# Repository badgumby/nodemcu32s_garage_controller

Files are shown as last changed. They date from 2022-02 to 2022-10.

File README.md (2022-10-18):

# NodeMCU-32s Garage Controller

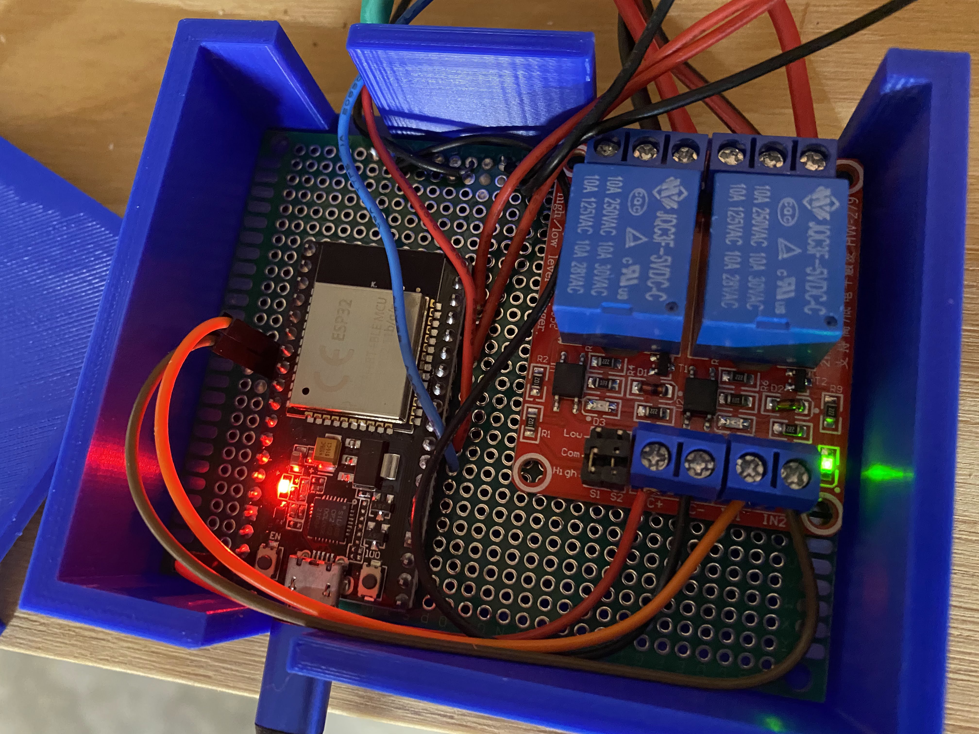
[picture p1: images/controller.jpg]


This project is still a WIP, so the code is yet to be optimized. The goal is to turn my two regular garage doors into "smart" garage doors. This controller will be the base platform using a NodeMCU-32s (or similarly cloned SoC).

## Materials

These are the items you may need to purchase to build this project.

### Devices/Sensors

- ESP32 Development Board
  - I used this one [KeeYees Development Board - ESP-WROOM-32 Chip](https://www.amazon.com/dp/B07QCP2451?psc=1&ref=ppx_yo2_dt_b_product_details)
  - But I also have this one, and it is better [DOIT DEVIT V1 ESP32-WROOM-32 Development Board](https://www.amazon.com/dp/B084KWNMM4?psc=1&ref=ppx_yo2_dt_b_product_details)

- Two magnetic reed switches
  - Similar item on Amazon: [Gikfun MC-38 Wired Door Sensor Magnetic Switch](https://www.amazon.com/dp/B0154PTDFI?psc=1&ref=ppx_yo2_dt_b_product_details)

- Two 5mm green LEDs (you can use pre-soldered LEDs with resistors, I believe mine were 460 ohm.)
  - Similar item on Amazon: [EDGELEC 56pcs (7 Colors x 8pcs)](https://www.amazon.com/EDGELEC-LED-Emitting-Assorted-Warm-White/dp/B07W4H66LR/)

- One 2-channel 5VDC relay module (high trigger)
  - Similar item on Amazon: [2 pcs 5V 2 Channel DC 5V Relay Module with Optocoupler High/Low Level Trigger](https://www.amazon.com/dp/B079FGPC9Y?psc=1&ref=ppx_yo2_dt_b_product_details)

### Misc Materials

- Speaker wire
  - Run from the relay to the garage door button sockets.
  - Similar item on Amazon: [TYUMEN 100FT 16 Gauge 2pin 2 Color Red Black Cable](https://www.amazon.com/dp/B07SG23DT1?psc=1&ref=ppx_yo2_dt_b_product_details)

- Printed circuit board
  - Just a generic PCB large enough to accommodate solder points for LEDs, relay leads, etc.
  - Similar item set on Amazon: [ELEGOO 32 Pcs Double Sided PCB Board Prototype Kit](https://www.amazon.com/dp/B072Z7Y19F?psc=1&ref=ppx_yo2_dt_b_product_details)

- 3D printer filament
  - The case for this project has been 3D printed, and I have provided the models along with the codebase. Please see the [Enclosure](#enclosure) section below.

## Schematic

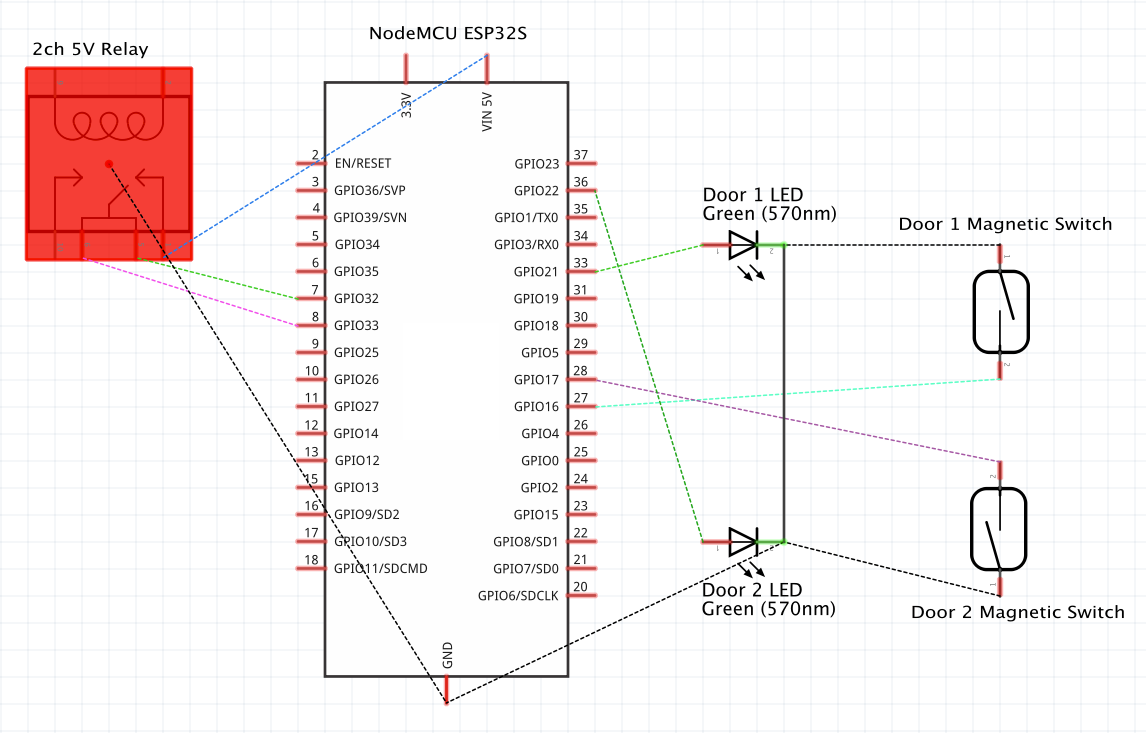
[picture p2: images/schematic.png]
Basic Schematic


Here is the schematic (created using Fritzing). Please note, the schematic does not have any resistors for the LEDs. This is because the LEDs I am using are pre-wired, and already have the correct resistors added for this voltage/amperage. Just don't forget to add some to your LEDs if you are not using pre-wired LEDs.

## Enclosure

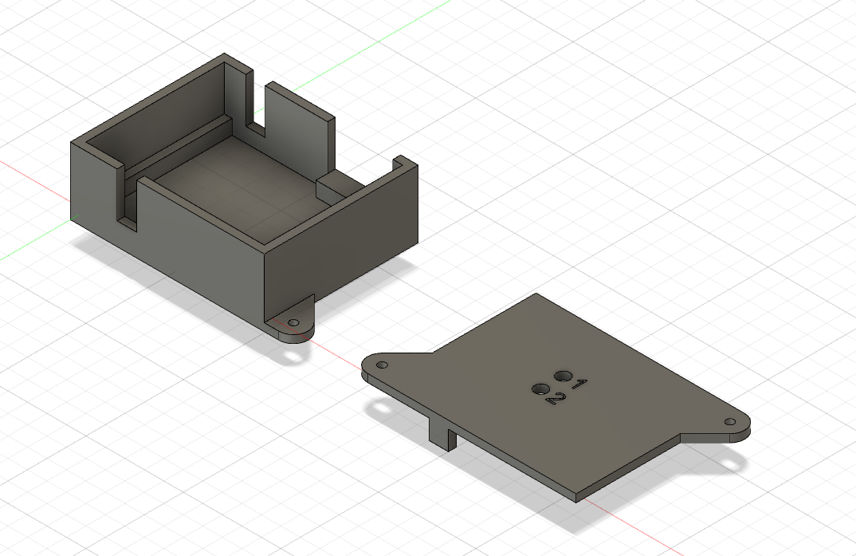
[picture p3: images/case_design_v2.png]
Fusion 360 model - v2


In this project, you will find the [STL files](/enclosure/STL/) for the top and bottom of the case, as well as, the [Fusion 360 model](/enclosure/Fusion%20360/) file. These can be used to 3D print the enclosure, or can be modified to fit your own project. It was designed around the 7cm x 9cm PCB linked in the [Misc Materials](#misc-materials) section above.

### 3D Print Settings

---

I have a Creality Ender 3 v2 with an upgraded Micro Swiss all-metal hotend, and these are the settings I used to print the enclosure (and most other things) in the [Cura slicing software](https://ultimaker.com/software/ultimaker-cura).

- Quality
  - Layer Height: 0.16 mm
  - Initial Layer Height: 0.2 mm
  - Line Width: 0.4 mm
  - Initial Layer Line Width: 100%
- Walls
  - Wall Thickness: 1.2 mm
    - Wall Line Count 3
  - Optimize Wall Printing Order: YES
  - Fill Gaps Between Walls: Everywhere
  - Horizontal Expansion: 0 mm
- Top/Bottom
  - Top/Bottom Thickness: 0.84 mm
  - Monotronic Top/Bottom Order: NO
  - Enable Ironing: NO
- Infill
  - Infill Density: 15%
    - Infill Line Distance 8.0 mm
  - Infill Pattern: Cubic
- Material (PLA)
  - Printing Temperature: 200° C
  - Build Plate Temperature: 60° C
- Speed
  - Print Speed: 50 mm/s
    - Infill Speed: 50 mm/s
    - Wall Speed: 25 mm/s
  - Travel Speed: 150 mm/s
  - Initial Layer Speed: 20 mm/s
- Travel
  - Enable Retraction: YES
  - Retract Layer Change: NO
  - Retraction Distance: 5 mm
  - Retraction Speed: 45 mm/s
  - Avoid Printed Parts When Traveling: YES
  - Avoid Supports When Traveling: YES
  - Travel Avoid Distance: 0.625 mm
  - Z Hop When Retracted: NO
- Cooling
  - Enable Print Cooling: YES
  - Fan Speed 100%
  - Regular/Maximum Fan Speed Threshold: 10s
  - Life Head: NO
- Support
  - Generate Support: NO
- Build Plate Adhesion
  - Build Plate Adhesion Type: None

## Home Assistant Configuration

To use this controller with [Home Assistant](https://home-assistant.io) you will need to configure an MQTT Broker. Here is a guide on configuring the integrated [MQTT Broker](https://www.home-assistant.io/docs/mqtt/broker/).

Once you have configured an MQTT Broker for use in Home Assistant, you will need to add the content below to your `configuration.yaml`, then restart Home Assistant.

```yaml
mqtt:
  cover:
    - command_topic: "gumby_garage/door_1_toggle"
      name: "Garage Door 1"
      payload_close: "close"
      payload_open: "open"
      device_class: garage
      position_topic: "gumby_garage/door_1_pos"
      unique_id: "garage_door_1"
    - command_topic: "gumby_garage/door_2_toggle"
      name: "Garage Door 2"
      payload_close: "close"
      payload_open: "open"
      device_class: garage
      position_topic: "gumby_garage/door_2_pos"
      unique_id: "garage_door_2"
```

Home Assistant should now be subscribed to the above topics, and will update the `cover.garage_door_1` and `cover.garage_door_2` objects with their statuses.

These can now be used with the automations provided in the [automations.yaml](/home-assistant/automations.yaml) file.

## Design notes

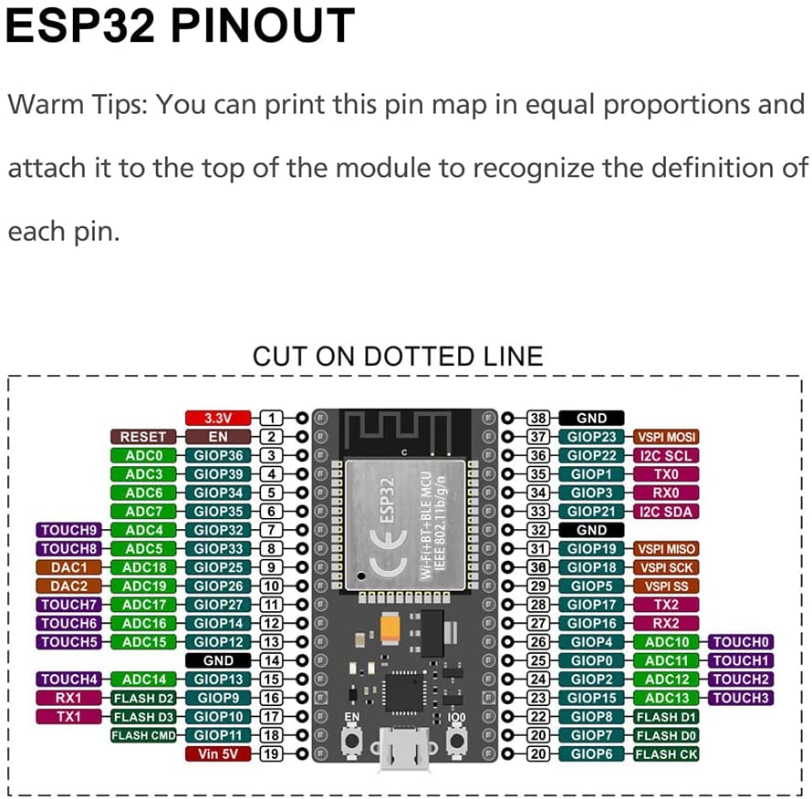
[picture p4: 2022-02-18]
images/esp32_pinout(node clone).jpg

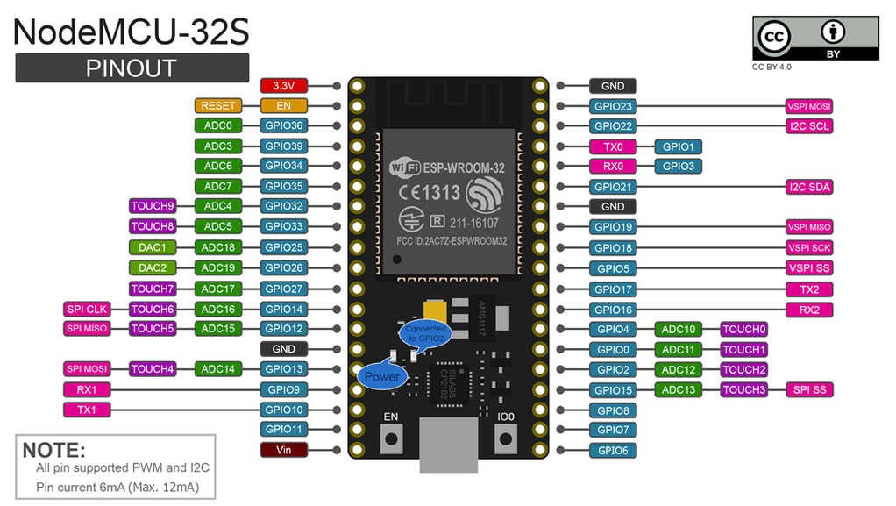
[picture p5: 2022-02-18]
images/nodemcu-32s.png

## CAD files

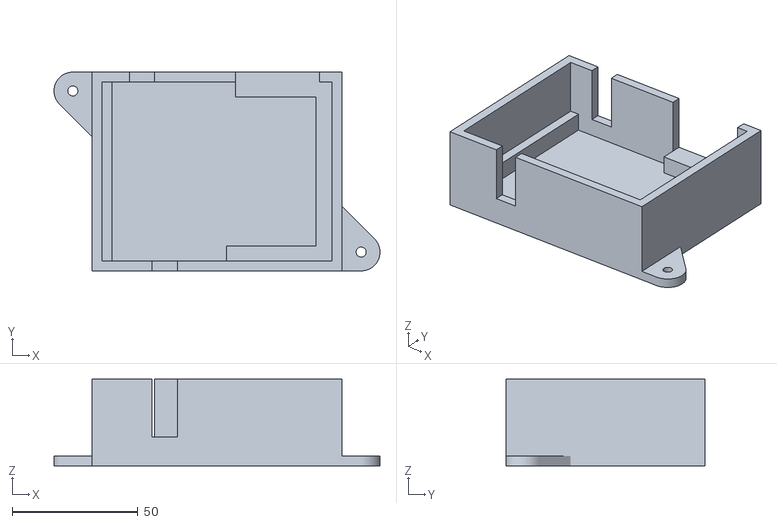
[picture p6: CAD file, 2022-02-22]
Enclosure/STL/bottom_v2.stl
129.5 x 79.0 x 34.5

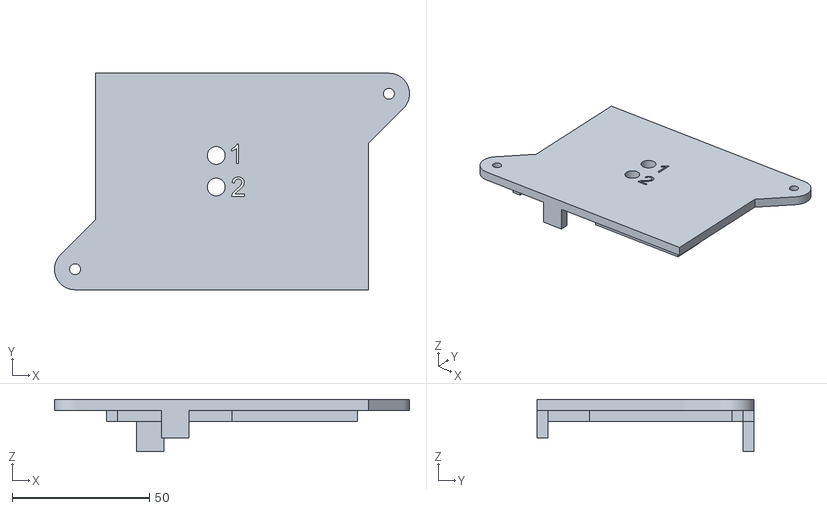
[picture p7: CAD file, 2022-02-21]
Enclosure/STL/top_v2.stl
129.5 x 79.0 x 19.0

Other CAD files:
Enclosure/Fusion 360/enclosure_v2.f3d

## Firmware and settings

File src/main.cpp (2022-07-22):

#include <Arduino.h>      // Used for Arduino framework (which ESP32 chips support)
#include <WiFi.h>         // Used to connect to WiFi
#include <PubSubClient.h> // Used for MQTT communication
#include "credentials.h"  // Header file containing wifi and HA creds

// If you don't want to WebSerial access, disable these headers, and any WebSerial print
// Also remove 'ESP Async WebServer' and 'ayushsharma82/WebSerial @ ^1.1.0' from the platformio.ini file
#include <AsyncTCP.h>
#include <ESPAsyncWebServer.h>
#include <WebSerial.h>

// Sensor pins
const int DOOR_1_PIN = 16; // Magnetic reed switch
const int DOOR_2_PIN = 17; // Magnetic reed switch
const int LED_1_PIN = 21; // LED used for Door 1
const int LED_2_PIN = 22; // LED used for Door 2
const int RELAY_1_PIN = 32; // Relay to toggle Door 1
const int RELAY_2_PIN = 33; // Relay to toggle Door 2

// Default states (0 = Closed, 1 = Open, 2 = Fetch new state)
int DOOR_1_STATE = 0;
int DOOR_2_STATE = 0;
int LAST_DOOR_1_STATE = 2;
int LAST_DOOR_2_STATE = 2;
int LOOP_COUNTER = 0; // This is used to send checkin every 15 seconds
int LOOP_COUNTER_WIFI = 0; // This is used to count how many times the Wifi has reconnected

// MQTT settings/topics
const char *ID = "gumby_garage_controller";  // Name of our device, must be unique
const char *REFRESH_LISTENER = "gumby_garage/refresh_status"; // Used to trigger a forced update
const char *DOOR_1_POS_TOPIC = "gumby_garage/door_1_pos"; // Position of Door 1
const char *DOOR_2_POS_TOPIC = "gumby_garage/door_2_pos"; // Position of Door 1
const char *DOOR_1_RELAY_TOPIC = "gumby_garage/door_1_toggle"; // Toggle door open/close
const char *DOOR_2_RELAY_TOPIC = "gumby_garage/door_2_toggle"; // Toggle door open/close

// Door position variables
const char *OPEN = "100";
const char *CLOSE = "0";

// Setup WiFi client
WiFiClient wclient;
// Setup MQTT client
PubSubClient client(wclient);
bool state=0;

// Function to toggle the doors
void ToggleDoor(int DOOR_RELAY, int WAIT, const char* TOPIC, const char* POSITION) {
  digitalWrite(DOOR_RELAY,HIGH); // Turn on relay
  delay(500); // Wait .5 seconds
  digitalWrite(DOOR_RELAY,LOW); // Turn off relay
  client.publish(TOPIC, POSITION); // Notify MQTT broker door should be closed
  delay(WAIT); // Wait for door to act
}

// WebSerial server setup
AsyncWebServer server(80);
// WebSerial callback message
void webSerialMsg(uint8_t *data, size_t len){
  WebSerial.println("Received Data...");
  String d = "";
  for(int i=0; i < len; i++){
    d += char(data[i]);
  }
  WebSerial.println(d);
}

// Print line to both Serial and WebSerial
template<class TYPE>
void DualSerial(TYPE MSG) {
  WebSerial.println(MSG);
  Serial.println(MSG);
}

void callback(char* topic, byte* payload, unsigned int length) {
  // Fetch current door states
  DOOR_1_STATE = digitalRead(DOOR_1_PIN);
  DOOR_2_STATE = digitalRead(DOOR_2_PIN);

  // Print topic and message to serial
  DualSerial("Topic: ");
  DualSerial(topic);
  DualSerial("Message: ");

  // Convert message from char* to string
  String message;
  for (int i = 0; i < length; i++) {
    message = message + (char)payload[i];
  }
  DualSerial(message);

  // Decision tree for received topic messages
  if (strcmp(topic, "gumby_garage/door_1_toggle")==0) {
    // If message is to close, and the door is currently open
    if(message == "close" && DOOR_1_STATE == 1) {
      ToggleDoor(RELAY_1_PIN, 15000, DOOR_1_POS_TOPIC, CLOSE);
      LAST_DOOR_1_STATE = 2; // Reset door state so void Loop can fetch new state
    }
    // If message is to open, and the door is currently closed
    if(message == "open" && DOOR_1_STATE != 1) {
      ToggleDoor(RELAY_1_PIN, 2000, DOOR_1_POS_TOPIC, OPEN);
      LAST_DOOR_1_STATE = 2; // Reset door state so void Loop can fetch new state
    } 
  } else if (strcmp(topic, "gumby_garage/door_2_toggle")==0) {
    // If message is to close, and the door is currently open
    if(message == "close" && DOOR_2_STATE == 1) {
      ToggleDoor(RELAY_2_PIN, 15000, DOOR_2_POS_TOPIC, CLOSE);
      LAST_DOOR_2_STATE = 2; // Reset door state so void Loop can fetch new state
    }
    // If message is to open, and the door is currently closed
    if(message == "open" && DOOR_2_STATE != 1) {
      ToggleDoor(RELAY_2_PIN, 2000, DOOR_2_POS_TOPIC, OPEN);
      LAST_DOOR_2_STATE = 2; // Reset door state so void Loop can fetch new state
    }
  } else if (strcmp(topic, "gumby_garage/refresh_status")==0) {
    DualSerial("Sending door state refresh...");
    LAST_DOOR_1_STATE = 2; // Reset door state so void Loop can fetch new state
    LAST_DOOR_2_STATE = 2; // Reset door state so void Loop can fetch new state
  } else {
    // Listening to topic, but can't something went wrong
    DualSerial("Error on topic: '");
    DualSerial(topic);
    DualSerial("' with message: ");
    DualSerial(message);

  }
 
  DualSerial("-----------------------");
 
}

// Reconnect to client
void reconnect() {
  // Loop until reconnected
  while (!client.connected()) {
    DualSerial("Attempting MQTT connection...");
    // Attempt to connect
    if (client.connect(ID,HA_USER,HA_PASS)) {
      DualSerial("connected");
      DualSerial("Publishing to the following topics: ");
      DualSerial(DOOR_1_POS_TOPIC);
      DualSerial(DOOR_2_POS_TOPIC);

    } else {
      DualSerial(" try again in 5 seconds");
      // Wait 5 seconds before retrying
      delay(5000);
    }
  }
  // MQTT subscription topics
  client.subscribe(REFRESH_LISTENER);
  client.subscribe(DOOR_1_RELAY_TOPIC);
  client.subscribe(DOOR_2_RELAY_TOPIC);
  DualSerial("-----------------------");
}

void initWiFi() {
  WiFi.mode(WIFI_STA);
  WiFi.begin(ssid, password);
  Serial.print("Connecting to WiFi ...");
  while (WiFi.status() != WL_CONNECTED) {
    Serial.print('.');
    delay(1000);
  }
  Serial.println(WiFi.localIP());
}

void setup() {
  // Start serial monitoring
  Serial.begin(115200);
  // Connect to wifi
  initWiFi();
  // WebSerial startup
  // Accessible at "<IP Address>/webserial" in browser
  WebSerial.begin(&server);
  WebSerial.msgCallback(webSerialMsg);
  server.begin();
  // Print IP to WebSerial
  WebSerial.println(WiFi.localIP());
  // Print out the RSSI (in dB)
  DualSerial(WiFi.RSSI());
  // Set pin modes
  pinMode(DOOR_1_PIN, INPUT_PULLUP);
  pinMode(DOOR_2_PIN, INPUT_PULLUP);
  pinMode(LED_1_PIN, OUTPUT);
  pinMode(LED_2_PIN, OUTPUT);
  pinMode(RELAY_1_PIN, OUTPUT);
  pinMode(RELAY_2_PIN, OUTPUT);
  // Start MQTT publisher
  client.setServer(broker, 1883);
  // Start MQTT subscriber
  client.setCallback(callback);
}

void loop() {
  // Restart if it has had to reconnect to Wifi more than 5 times
  if (LOOP_COUNTER_WIFI >= 5) {
    ESP.restart();
  }
  // Reconnect if connection is lost
  if (!client.connected()) {
    reconnect();
    LOOP_COUNTER_WIFI++;
  } 

  client.loop();

  // Increment loop counter
  LOOP_COUNTER++;

  // Read current door states
  DOOR_1_STATE = digitalRead(DOOR_1_PIN);
  DOOR_2_STATE = digitalRead(DOOR_2_PIN);

  // Monitor magnet switch for Door 1
  if (DOOR_1_STATE != LAST_DOOR_1_STATE) {
    if (DOOR_1_STATE == 1) {
      digitalWrite(LED_1_PIN, HIGH); // LED On
      DualSerial("Door 1: open"); // Print status to serial monitor
      client.publish(DOOR_1_POS_TOPIC, "100"); // MQTT Door 1 open
    } else {
      digitalWrite(LED_1_PIN, LOW); // LED Off
      DualSerial("Door 1: closed"); // Print status to serial monitor
      client.publish(DOOR_1_POS_TOPIC, "0"); // MQTT Door 1 closed
    }
  }
  
  // Monitor magnet switch for Door 2
  if (DOOR_2_STATE != LAST_DOOR_2_STATE) {
    if (DOOR_2_STATE == 1) {
      digitalWrite(LED_2_PIN, HIGH);  // LED On
      DualSerial("Door 2: open"); // Print status to serial monitor
      client.publish(DOOR_2_POS_TOPIC, "100"); // MQTT Door 2 open
    } else {
      digitalWrite(LED_2_PIN, LOW); // LED Off
      DualSerial("Door 2: closed"); // Print status to serial monitor
      client.publish(DOOR_2_POS_TOPIC, "0"); // MQTT Door 2 closed
    }
  }

  // Check loop counter for MQTT checkin interval
  // This is useful for sending updates in case Home Assistant has restarted
  // Sometimes Home Assistant will put a device in an unknown state on HA startup, and will not update it's state until it's received a new message
  if (LOOP_COUNTER >= 30) {
    LAST_DOOR_1_STATE = 2; // Force door state fetch on next loop
    LAST_DOOR_2_STATE = 2; // Force door state fetch on next loop
    LOOP_COUNTER = 0; // Reset loop counter
  } else {
    LAST_DOOR_1_STATE = DOOR_1_STATE; // Update previous door state to current door state
    LAST_DOOR_2_STATE = DOOR_2_STATE; // Update previous door state to current door state
  }
  
  delay(500); // Wait .5 seconds before restarting the loop
}

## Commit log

2022-02-20 updated readme with Amazon links and switched relay pins from GPIO 2/4 to 32/33
2022-02-21 update readme and include model files
    [bottom_v1.stl, enclosure_v1.f3d, top_v1.stl]
2022-02-21 corrected issue with inverse lid. added screw holes for mounting thru lid
    [bottom_v2.stl, enclosure_v2.f3d, top_v1.stl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]
2022-02-21 add 12 second delay on close, and update readme for 5mm LEDs
2022-02-22 update image and add v2 of case
    [bottom_v2.stl, enclosure_v1.f3d, enclosure_v2.f3d]
2022-02-22 update readme and add schematic image
2022-02-22 update schematic image
2022-02-22 add 3D print settings to readme
2022-02-22 created function ToggleDoor() and replaced duplicative code with this function.
    [main.cpp]
2022-02-25 add WebSerial to device for remote debugging
2022-07-22 Added autoreset after multiple wifi reconnect failures - This fixes an issue when my wifi goes offline and causes the ESP to lock up
    [main.cpp]
2022-10-18 update configuration yaml info to new format requirements for MQTT devices
